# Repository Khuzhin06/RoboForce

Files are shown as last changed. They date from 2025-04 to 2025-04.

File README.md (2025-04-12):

# RoboForce

Всем привет! Давно хотели собрать своего робота? Не слышали про ROS? Не знаете с чего начать?

Тогда вы не зря зашли к нам, мы постараемся максимально подробно и быстро рассказать о нашем пути создания робота на ROS2 Jazzy и esp32,по этим материалам вы с легкостью сможете повторить этот проект. 

Ну а если вы хотите с головой погрузится в мир увлекательной робототехники и разобраться во всех тонкостях, то проходите курс на stepik - https://stepik.org/course/221157/syllabus Все материалы, используемые в этой статье были взяты из этого курса и мы лишь делимся опытом создания робота и проблемами с которыми столкнулись мы. 

Проблемы при сборки робота - это неотъемлемая часть процесса, поэтому мы постарались описать решение всех проблем с которыми мы сталкивались в процессе сборки и программирования робота.

Также много интересной, полезной и актуальной информации можете найти в нашем TG-канале https://t.me/RoboForc 

# Содержание:

[I модуль - Сборка робота](#i-модуль---сборка-робота)
- [1. Подготовка материалов и инструментов](#1-подготовка-материалов-и-инструментов)
- [2. Изготовление корпуса](#2-изготовление-корпуса)
  - [Шаг 1: Резка деталей](#шаг-1-резка-деталей)
  - [Шаг 2: 3D-печать](#шаг-2-3d-печать)
  - [Шаг 3: Сборка каркаса (первый слой)](#шаг-3-сборка-каркаса-первый-слой)
  - [Шаг 4: Сборка каркаса (средний слой)](#шаг-4-сборка-каркаса-средний-слой)
  - [Шаг 5: Соединение нижней и средней платформ](#шаг-5-соединение-нижней-и-средней-платформ)
  - [Шаг 6: Тестовый запуск](#шаг-6-тестовый-запуск)  

[II Модуль - Программировоние ESP32](#ii-модуль-программирование-esp32)
- [1. Настройка моторов](#1-настройка-моторов)
- [2. Загрузка основной программы на ESP32](#2-загрузка-основной-программы-на-esp32)  

[III Модуль - Настройка и программирование верхнего уровня](#iii-модуль-настройка-и-программирование-верхнего-уровня)
- [1. Установка ubuntu](#1-установка-ubuntu)
- [2. Установка ROS2](#2-установка-ros2)
- [3. Настройка необходимых пакетов](#3-настройка-необходимых-пакетов)

# I Модуль - Сборка робота

## 1. Подготовка материалов и инструментов
Необходимые инструменты:
- Лазерный резак – для резки фанеры
- Дрель и сверла (2–3мм) – для отверстий
- Набор отверток с разными насадками
- Паяльник (40 Вт) + припой (POS-60) – для электроники
- Мультиметр – проверка цепей
- Наждачка - для обработки краёв деталей после резки.

Материалы и комплектующие:  

| Компонент | Описание | Кол-во | Ссылка | Стоимость |
| --- | --- | --- | --- |--- |
| Фанера | Толщина 6 мм, 600х600 | 1 лист | https://www.ozon.ru/product/fanera-9-mm-sort-3-3-600h600-mm-1869700011/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 | 370 |
| Винты М3 (+ гайки М3)| 30шт х 20мм, 4шт х 30мм, 4шт х 50мм | 38 | https://aliexpress.ru/item/1005005552471765.html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 | 160 |
| Винты М2.5 (+ гайки М2.5) | 2шт х 10мм | 2 | https://aliexpress.ru/item/1005005552471765.html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 | 150 |
| Винты М2 (+ гайки М2)| 4 шт х 10мм | 4 | https://aliexpress.ru/item/1005005552471765.html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 | 120 |
| Муфты  | Необходимы для закрепления колес на валах моторов | 2 | https://aliexpress.ru/item/1005004333022107.html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 | 420 |
| OMNI-колесо | Позволяет двигаться роботу в любом направлении ьез поворота основных колес | 1 | https://aliexpress.ru/item/1005008405743640.html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 | 1540 |
| Микрокомпьютер Raspberry pi 5 8gb | «Верхний уровень». Обрабатывает информацию, поступающую с ESP (“нижнего уровня»). Поддержка новейших интерфейсов. Отлично подходит к задачам компьютерного зрения, обработки данных с лидаров.  | 1 | https://sl.aliexpress.ru/p?key=0vxkGbg | 10000 |
| Микроконтроллер ESP32-WROOM-32 | «Нижний уровень». Собирает информацию с датчиков, энкодеров и отправляет на «верхний уровень». Подходит для сетевого проекта из-за встроенных Wi-Fi и Bluetooth, высокой производительности и большого объёма памяти. | 1 | https://sl.aliexpress.ru/p?key=7oxkGZr | 300 |
| Моторы JGA25-370 77 RPM 12 B | Необходимы для передвижения робота. Используем 12В для упрощения питания. | 2 | https://aliexpress.ru/item/1005007793208347.html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 | 1200 |
| Драйвер моторов L298N | Необходим для управления моторов. | 1 | https://aliexpress.ru/item/1005007125159518.html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 | 150 |
| Понижающие DC-DC преобразователи Readytosky FPV RC UBEC 5V 5A | Обеспечивает стабильное питание для микроконтроллера, микрокомпьютера, датчиков и драйверов. Имеет удобный форм-фактор и изолированный корпус. | 2 | https://aliexpress.ru/item/33019505937.html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 | 530 |
| Литиевые батареи JOUYM 18650, 2000 мАч | Обеспечивает питание робота. Обладают высокой плотностью энергии при относительно небольшом размере. Можно последовательно соединять несколько штук, добиваясь нужного напряжения. | 3 | https://sl.aliexpress.ru/p?key=ajxkGkw | 460 |
| Держатель для батарей | Корпус для уставноки литейных батареек | 1 | https://aliexpress.ru/item/1005005586103501.html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 | 140 |
| Лидар SLAMTEC RPLIDAR C1 | «Глаза» робота, который смотрит на окружение, вычисляет расстояние на 360 градусов вокруг, определяет препятствия впереди | 1 | https://sl.aliexpress.ru/p?key=fmxkGwR | 6740 |
| Штыревые штекеры и гнезда | Служат для удобства работы с микроконтроллером, его легкой замены - провода припаиваются не к самому МК, а к штекерам. | 2х2 | https://aliexpress.ru/item/1005004954771161.html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 | 200 |
| Комплект разъемов | Нужны для соединения электронной схемы без пайки. | 1 | https://aliexpress.ru/item/1005007622670523.html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 | 120 |

СТОИМОСТЬ КОМПОНЕНТОВ ДЛЯ СБОРКИ РОБОТА:

За относительно небольшой бюджет можно также собрать достаточно надежного и производительного робота.
Суммируя все цены комплектующих из I модуля 1 пункта, мы получаем итоговую стоимость нашей модели - 22.600 рублей (на момент 06.04.2025).

## 2. Изготовление корпуса

### Шаг 1: Резка деталей
Загрузите DXF-файлы в станок лазерной резки.  
Основные детали:
- Основание (нижняя платформа)
- Средняя платформа
- Крышка (верхняя платформа)
- 2 опоры для OMNI колеса
- 5 стоек по 60 мм
- 4 стойки по 130 мм
После резки обработайте края наждачкой, чтобы избежать заусенцев.  

### Шаг 2: 3D-печать
Загрузите stl-файлы в станок 3D-печати.  
Основные детали:  
- 2 колеса
- Стойки для моторчиков



### Шаг 3: Сборка каркаса (первый слой)
1. Установка мотор редукторов
На валы мотор-редукторов установите колёса с помощью муфт (2 шт) и винтов М3 (2 шт), закрепите их стопорными винтами.


Найдите на нижней платформе посадочные места под моторы.
Зафиксируйте каждый мотор винтами M3 х 50 мм (4 шт) и гаек М3 (4 шт) с помощью напечатанных стоек (обратите внимание на то, чтобы провода от энкодеров были выведены к центру платформы)
Убедитесь, что при вращении колёса не задевают за край платформы и установлены ровно.
Уделите внимание ровной установке колес, это обеспечит качественное движение без лишних корректировок.



2. Установка OMNI колеса 
Найдите на нижней платформе посадочные места под вырезанные опоры OMNI колеса.
Установите их с помощью винтов М3 х 20 (4 шт) и гаек М3 (4 шт)



Закрепите OMNI колесо винтами М3 (2 шт).
Убедитесь, что при вращении колёсо не задевает за край платформы.

3. Установка драйвера моторов
Найдите в центре нижней платформы посадочные места под драйвер
Установите драйвер с помощью винтов М3 (2шт) и гаек М3 (2шт)


### Шаг 4: Сборка каркаса (средний слой)
1. Пайка шилда для ESP
Шилд – плата с контактными площадками.   
Установите на ESP штыревые гнезда, затем вставьте конструкцию в печатную плату (со стороны пайки)

Установите штыревые штекеры в средних с конструкцией линиях на плате.
Аккуратно переверните плату, поддерживая все компоненты.


Включите паяльник и дождитесь, пока инструмент разогреется до 300-350°C. 
Нанесите припой на крайние контакты (используйте флюс для лучшего растекания припоя)
Необходимо спаять все крайние контакты попарно (контакт гнезда с контактом штекера)
Проведите аналогичную работу со всеми оставшимися контактами (ВАЖНО: два спаянных контакты не должны быть соединены с соседними. 


После окончания пайки необходимо провести проверку: 
А. Визуальный осмотр:  
   - Нет ли перемычек между контактами (проверка на отсутствие короткого замыкания)
 Все ли дорожки пропаяны (особенно у штыревых разъёмов).  
Б.  Тест мультиметром:  
   - Прозвоните линии 5V и 3.3V на КЗ.  
   - Проверьте контакты GPIO на обрыв.

2. Установка шилда на платформу
Найдите на средней платформе посадочное место для шилда
Вставьте снизу в платформу винты М2 (4шт) и накрутите на них гайки М2 (4шт). Данная конструкция не позволит передать находящиеся под шилдом провода  
Установите на винты собранный шилд и закрепите его сверху гайками М2 (4шт)


3. Установка блока питания
Найдите на средней платформе посадочное место для блока питания (средняя часть платформы) 
Закрепите блок с помощью винтов М3 (2 шт) и гаек М3 (2шт)  (ВАЖНО: провода должны выходить в центральную часть платформы)


4. Монтаж:
   макетную и монтажную схему можно подробно изучить в папке Electronic scheme
Электрическая схема:


Пайка проводов, преобразователей, RGB ленты, драйвера, энкодеров, микроконтроллера.
Залудите контакты перед пайкой, а затем работайте по тому же принципу, как и при пайке шилда  
После окончания пайки необходимо провести проверку (визуальный осмотр и тест мультиметром) (ВАЖНО: проверьте, нет ли пережатых проводов)



### Шаг 5: Соединение нижней и средней платформ
Соберите стойки из фанеры: 5 штук по 60 мм, 4 штуки по 130 мм (для этого понадобятся гайки М3 18 шт)
Соедините нижнюю и верхнюю платформы с помощью стоек по 60 мм, винтов М3 (10шт)






### Шаг 6: Тестовый запуск
- Подключите питание. 
- Проверьте работу моторов, питание и загрузку ESP.
- Проанализируйте, движится ли робот в заданном вами направлении или нет.
ВАЖНО: есть вероятность, что робот поедет в обратную сторону, так как у него 2 шнура, которые можно перепутать местами. В таком случае необходимо поменять местами номера бортов в коде и загрузить его. Теперь робот поедет в заданном вами направлении.
- Измерьте количество тиков и запишите их в программу.


![Uploading image.png…]()

# II Модуль - Программирование ESP32

После того как вся аппаратная часть собрана, можно переходить и к программной.
Все действия лучше делать на ноутбуке - так как это будет быстрее и надежней, хотя в теории можете и сделать все тоже самое на raspberry.
Начнем с программирования "нижнего уровня", тоесть esp32. Программировать будем через arduino IDE (если она еще у вас не установлена, то можете скачать с официального сайта https://www.arduino.cc/en/software ).
Чтоб можно было прошивать нашe платe добавим ее в список доступных для прошивки. Нужно зайти в файл->настройки и в поле "Дополнительные менеджеры плат" вставляем ссылку: https://raw.githubusercontent.com/espressif/arduino-esp32/gh-pages/package_esp32_index.json и нажимаем "ОК". 
После заходим в инструменты->плата->менеджер плат тут в строке поиска вводим esp32, выбираем соответсвующий вариант снизу и нажимаем на кнопку установить. 
После всех этих процедур для прошивки станут доступны платы семейства  ESP32.  Чтоб выбрать нужную плату заходим в инструменты->esp32 и выбираем нужную плату (мы использовали "ESP32 dev Module"). Также необходимо подключить саму плату к компьютеру и выбрать порт к которому она подключена заходим опять в инструменты->порт и выбираем нужный порт.
Помимо этого необходимо установить библиотеку для адресной светодиодной ленты. Для этого заходим в скетч->подключить библиотеку->Управлять библиотеками в поле поиска вводим "neopixel" и выбираем Adafruit neopixel и нажимаем установить.

## 1. Настройка моторов

Здесь нам нужно понять как подключены моторы и сделать так, чтоб робот ехал вперед, когда мы действительно этого хотим.

-проверить направление вращения моторов
-проверить подключение энкодеров

Скачиваем или копируем код для esp32 из папки low_level "test_move_esp32", открфываем этот код в arduino ide и нажимаем в правом верхнем углу "загрузить".

После полной загрузки кода колеса робота должны вращаться вперед, если это не так, то следует поменять в коде местами номера пинов, к которым подключён драйвер моторов левой или право стороны.
Для определения вращения энкодеров открываем в arduino IDE serial port и следим за значениями: оба значения на левом и правом моторах должны возрастать, если это не так, то меняем местами пины энкодера в программе.

## 2. Загрузка основной программы на ESP32.

Для этого шага нам необходимо скопировать все параметры из прдыдущего кода, а также измерить диаметр колеса и расстояние между центрами колёс.
Все эти параметры вашего робота необходимо внести в скетч main_esp32.ino, который находится в папке low-level. Этот код вы также скачиваете (или копируете) и открываете в Arduino IDE для дальнейшей прошивки. После внесения всех изменений в вашу программу по аналогии с 1 шагом загружаем программу на  микроконтроллер.

# III Модуль - Настройка и программирование верхнего уровня

До запуска робота остался последний и самый ответственный шаг. Настройка микрокомпьютера - наших "мозгов" робота. В нашем проекте эту роль выполняла raspberry pi 5 8gb, поэтому советуем все повторять на таком же железе для предотвращения проблем. Безусловно, подойдет и другое железо, по типу repka pi, orange pi, banana pi и подобных "фруктов". Но наиболее популярной и поддерживаемой всетаки остается "малинка".

## 1. Установка ubuntu

По сути raspberry pi является аналогом вашего ноутбука или настольного компьютера, но куда меньших размеров и, скорее всего, хуже по вычислительным мощностям. Но тем не менее нам нужно поставить на наш микрокомпьютер операционную систему - наиболее подходящая ubuntu 24.04. !!! при сборке нашего робота мы сначала поставили 24.10 - по принципу: больше - лучше, но тут,увы, так не работает. И чтобы у вас без проблем все встало как нужно необходимо использовать именно ubuntu 24.04 LTS!!! 
Скачать ее можно с официального сайта - она абсолютно бесплатная. После загрузки образа диска необходимо его записать на sd карту, которая будет стоять в малинке. Мы использовали на 64гб. Или же можно сразу скачать Raspberry PI Imager(https://www.raspberrypi.com/software/) и там уже в интерфейсе выбрать нужную операционную систему и ваш носитель.

## 2. Установка ROS2

После установки и базовых настроек операционной системы можно установить и сам ros2 jazzy (в нашем проекте используется десктопная версия ros-jazzy-desktop), лучше всего брать команды для установки с официального сайта (https://docs.ros.org/en/jazzy/Installation/Ubuntu-Install-Debs.html), так как они могут меняться. 

Если установить не получается пробуем еще раз, внимательно копируем все и вставляем в терминал. Если совсем не помогает, то можно попытаться погуглить ошибку, которую вам выдает терминал или же переустановить заново операционку на флешку и убедится что это точно ubuntu 24.04 LTS.

Также установим еще пару пакетов:

```
sudo apt install python3-pip
```

```
pip3 install setuptools
```

```
sudo apt install python3-colcon-common-extensions
```

## 3. Настройка необходимых пакетов

После установки ros2 в домашнеq директории нужно создать папку где будут хранится все наши пакеты для ros2.

```
mkdir ros2_ws
```

```
cd ros2_ws
```

```
mkdir src
```

```
cd-
```

```
colcon build
```

после создания нашего рабочего пространства
создадим пакет, который будет считывать сообщения из топика /cmd_vel

```
cd ~/ros2_ws/src
ros2 pkg create robot_control --build-type ament_python --dependencies rclpy geometry_msgs
cd robot_control/robot_control
```

создаем файл robot_controller_node.py и копируем в него код из одноименного файла папки high_level. Предварительно также нужно подключить прошитую esp32 к одному из портов raspberry pi, а затем ввести команду: 
```
ls -l /dev/serial/by-path/
```

после необходимо скопировать путь и заменить его в коде.
сохраняем файл. Делаем скрипт исполняемым:
```
chmod +x robot_controller_node.py
```

Далее находим и редактируем файл setup.py в этом пакете (нужно добавить 3-ю строчку):

```
entry_points={
    'console_scripts': [
        'robot_controller_node = robot_control.robot_controller_node:main',
    ],
},
```

Затем пересоберем наш пакет и установим все зависимости:

```
cd ~/ros2_ws
colcon build
source install/setup.bash
```

И запускаем наш пакет:

```
ros2 run robot_control robot_controller_node
```

Проверяем список топиков в другом терминале, должен появиться топик /cmd_vel

```
source /opt/ros/jazzy/setup.bash
ros2 topic list
```

Если топик появился, то все прошло успешно и мы можем управлять нашим роботом с клавиатуры!

Для этого установим пакет:

```
sudo apt install ros-jazzy-teleop-twist-keyboard
```
И запускаем пакет: 
```
ros2 run teleop_twist_keyboard teleop_twist_keyboard
```
Теперь робот должен ехать! Поздравляю мы проделали большой путь и запустили робота!

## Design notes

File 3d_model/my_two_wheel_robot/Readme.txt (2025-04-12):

Для запуска пакета его нужно скачать в директорию ros2_ws/src/. Затем в директории ros2_ws/ выполнить сборку пакета командой - colcon build, и подключив все зависимости - source install/setup.bash и source /opt/ros/jazzy/setup.bash , затем запустить сам пакет: ros2 launch my_two_wheel_robot two_wheel_robot.launch.py

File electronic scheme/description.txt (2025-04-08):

В данном документе можно изучить принципиальную, монтажную и макетную схему электронной цепи нашей модели робота 

  1 На макетной схеме вы сможете увидеть все комплектующие и их подключение

  2 На монтажной сможете увидеть их расположение между собой в самом роботе

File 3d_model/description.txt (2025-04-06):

Для разработки данной моедли робота необходимо:
 1) Распечатать 3D модели для колесной базы:
        а) колеса - 2 штуки
        б) крепежи для колес верхние - 2 штуки
        в) крепежи для колес нижние - 2 штуки
 2) вырезать корпус робота:
        а) основание 1 этажа робота

        б) основания 2 и 3 этажа робота ( 2 штуки)

        в)элемент стойки ( 9 пар по 2 штуки)

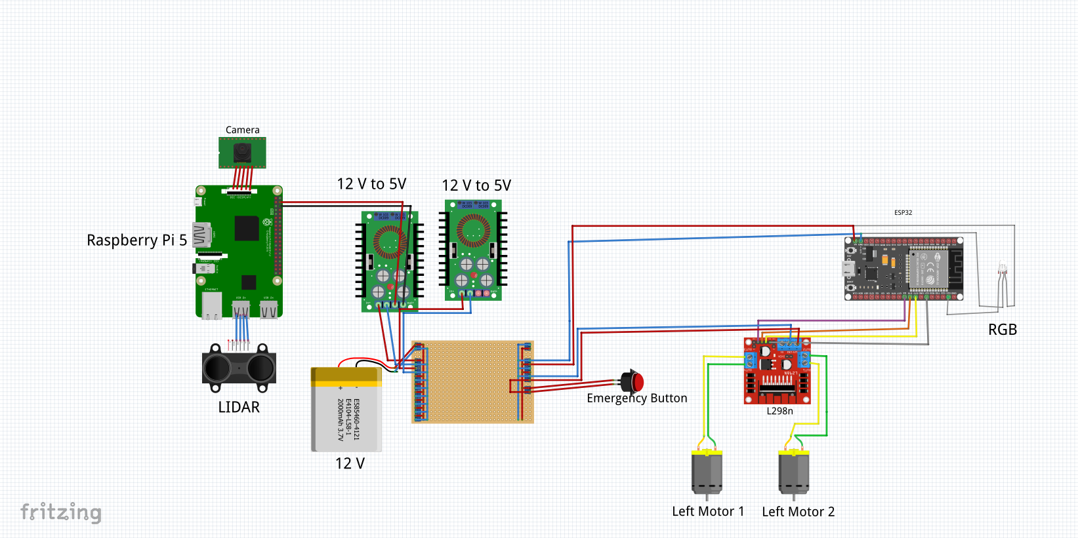
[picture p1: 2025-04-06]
electronic scheme/electronic_schem.png

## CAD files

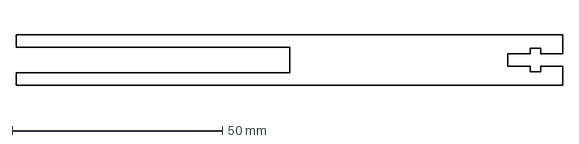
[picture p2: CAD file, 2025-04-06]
3d_model/6mm/LayerSupport130.dxf
130.0 x 12.0 mm

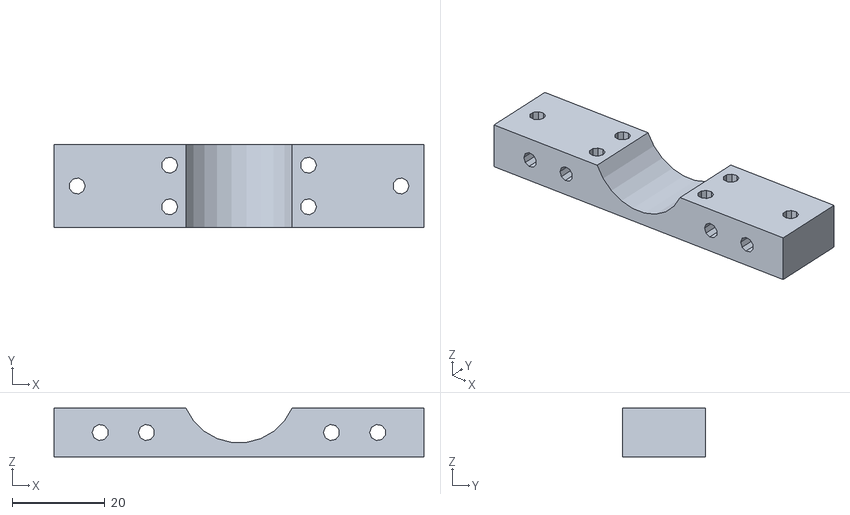
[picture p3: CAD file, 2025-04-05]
3d_model/krep_motor_niz_RoboForce.stl
80.0 x 18.0 x 10.5

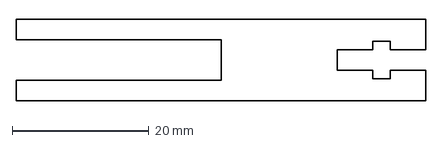
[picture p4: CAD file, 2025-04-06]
3d_model/6mm/LayerSupport65.dxf
60.0 x 12.0 mm

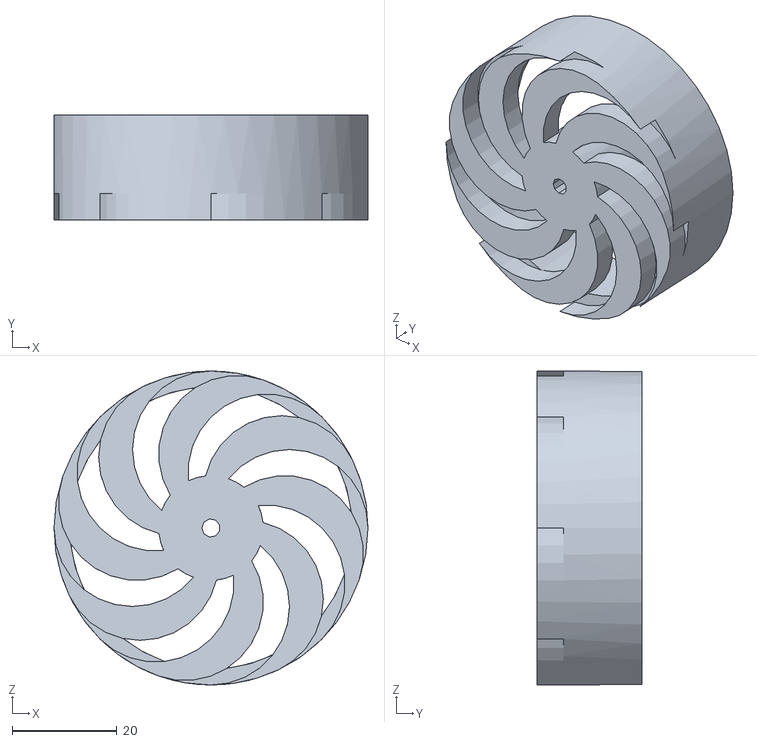
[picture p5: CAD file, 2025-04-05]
3d_model/wheel_RoboForce.stl
60.0 x 20.0 x 60.0

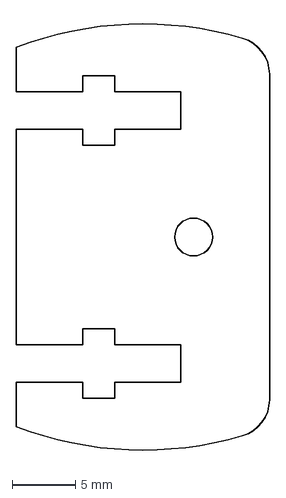
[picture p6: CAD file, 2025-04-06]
3d_model/6mm/OMNISupport.dxf
20.0 x 34.9 mm

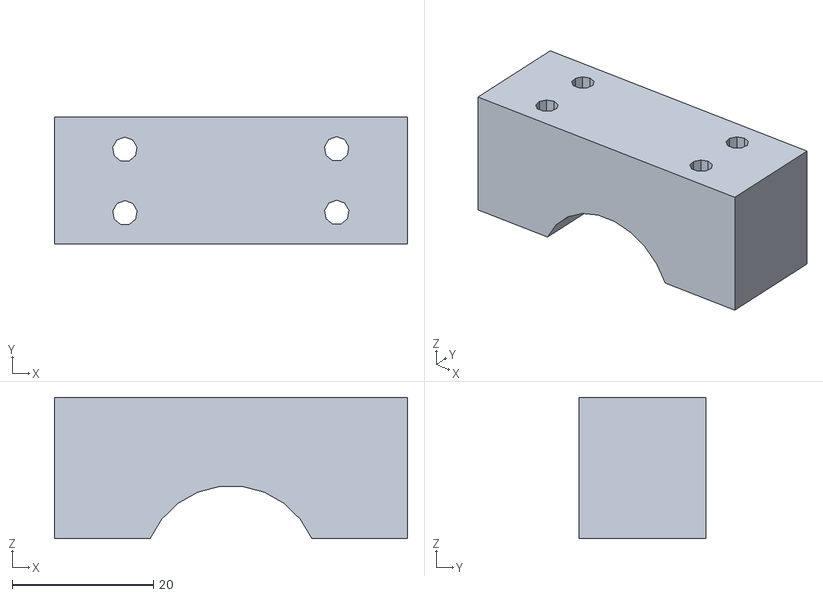
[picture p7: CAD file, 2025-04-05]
3d_model/krepMotor_verh_RoboForce.stl
50.0 x 18.0 x 20.0

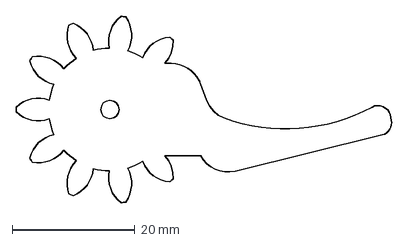
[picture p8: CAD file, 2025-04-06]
3d_model/6mm/GripperRightGear.dxf
61.4 x 30.4 mm

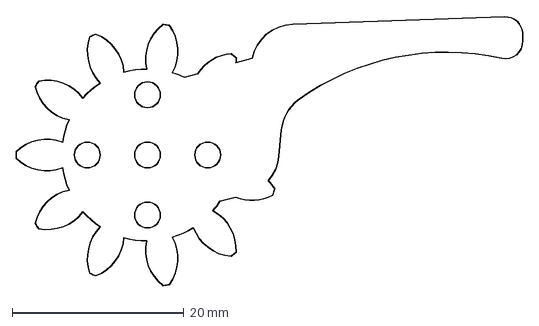
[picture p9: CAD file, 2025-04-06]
3d_model/6mm/GripperLeftGear.dxf
59.0 x 31.3 mm

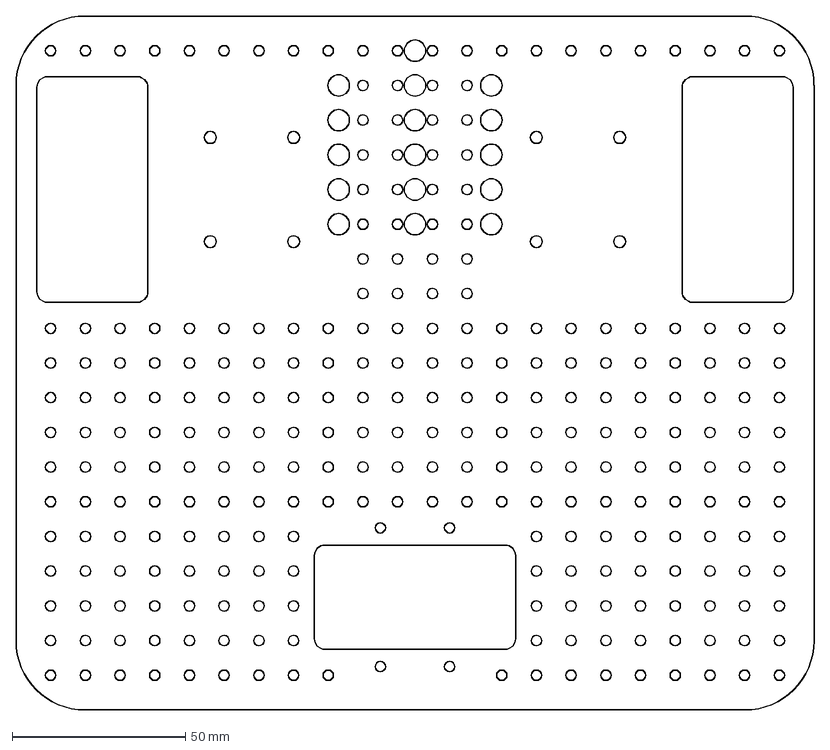
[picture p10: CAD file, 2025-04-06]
3d_model/6mm/BaseLayer.dxf
230.0 x 200.0 mm

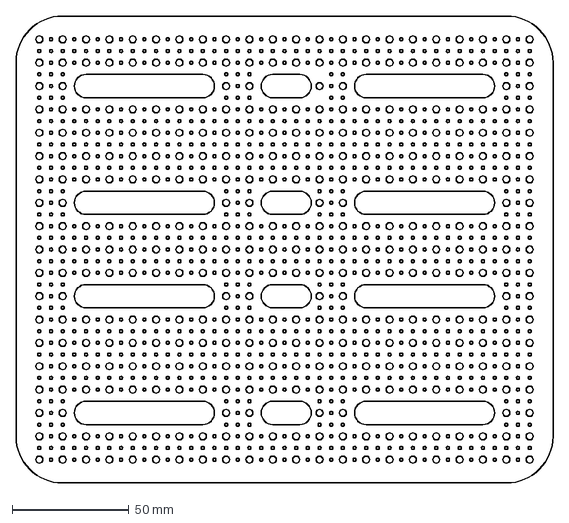
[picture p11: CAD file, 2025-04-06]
3d_model/6mm/Layer.dxf
230.0 x 200.0 mm

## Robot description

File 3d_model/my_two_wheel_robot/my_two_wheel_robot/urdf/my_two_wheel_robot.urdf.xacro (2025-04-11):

<?xml version="1.0"?>
<robot name="visual">

  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
  <link name="odom"/>

  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
  <link name="base_link">
    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
    <inertial>
      <mass value="1.5"/>
      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
    </inertial>
  </link>
  <joint name="base_link_joint" type="fixed">
    <parent link="odom"/>
    <child link="base_link"/>
    <origin xyz="0 0 0" rpy="0 0 0"/>
  </joint>
  
    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
  <link name="rod_front_left">
    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
    <inertial>
      <mass value="0.05"/>
      <origin xyz="0.09 0.105 0.095" rpy="0 0 0"/>
      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
    </inertial>
  </link>
  <joint name="rod_front_left_joint" type="fixed">
    <parent link="base_link"/>
    <child link="rod_front_left"/>
    <origin xyz="0 0 0" rpy="0 0 0"/>
  </joint>

  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
  <link name="rod_front_right">
    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
    <inertial>
      <mass value="0.05"/>
      <origin xyz="0.09 -0.105 0.095" rpy="0 0 0"/>
      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
    </inertial>
  </link>
  <joint name="rod_front_right_joint" type="fixed">
    <parent link="base_link"/>
    <child link="rod_front_right"/>
    <origin xyz="0 0 0" rpy="0 0 0"/>
  </joint>

  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
  <link name="rod_rear_left">
    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
    <inertial>
      <mass value="0.05"/>
      <origin xyz="-0.09 0.105 0.095" rpy="0 0 0"/>
      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
    </inertial>
  </link>
  <joint name="rod_rear_left_joint" type="fixed">
    <parent link="base_link"/>
    <child link="rod_rear_left"/>
    <origin xyz="0 0 0" rpy="0 0 0"/>
  </joint>

  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
  <link name="rod_rear_right">
    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
    <inertial>
      <mass value="0.05"/>
      <origin xyz="-0.09 -0.105 0.095" rpy="0 0 0"/>
      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
    </inertial>
  </link>
  <joint name="rod_rear_right_joint" type="fixed">
    <parent link="base_link"/>
    <child link="rod_rear_right"/>
    <origin xyz="0 0 0" rpy="0 0 0"/>
  </joint>

  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
  <link name="left_base">
    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
  </link>
  <joint name="left_base_joint" type="fixed">
    <parent link="base_link"/>
    <child link="left_base"/>
    <origin xyz="0.05 0.13 0" rpy="0 0 0"/>
  </joint>
  <link name="left_wheel">
    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
    <inertial>
      <mass value="1"/>
      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
    </inertial>
  </link>
  <joint name="left_wheel_joint" type="continuous">
    <axis xyz="0 1 0"/>
    <parent link="left_base"/>
    <child link="left_wheel"/>
    <origin xyz="0 0 0" rpy="0 0 0"/>
    <command_interface name="velocity"/>
    <state_interface name="position"/>
    <state_interface name="velocity"/>
  </joint>

  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
  <link name="right_base">
    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
  </link>
  <joint name="right_base_joint" type="fixed">
    <parent link="base_link"/>
    <child link="right_base"/>
    <origin xyz="0.05 -0.13 0" rpy="0 0 0"/>
  </joint>
  <link name="right_wheel">
    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
    <inertial>
      <mass value="1"/>
      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
    </inertial>
  </link>
  <joint name="right_wheel_joint" type="continuous">
    <axis xyz="0 1 0"/>
    <parent link="right_base"/>
    <child link="right_wheel"/>
    <origin xyz="0 0 0" rpy="0 0 0"/>
    <command_interface name="velocity"/>
    <state_interface name="position"/>
    <state_interface name="velocity"/>
  </joint>

  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
  <link name="caster_wheel">
    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
    <inertial>
      <mass value="0.1"/>
      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
    </inertial>
  </link>
  <joint name="caster_wheel_joint" type="fixed">
    <parent link="base_link"/>
    <child link="caster_wheel"/>
    <origin xyz="-0.09 0 -0.01" rpy="0 0 0"/>
  </joint>

  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
  <link name="electronics_plate">
    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
    <inertial>
      <mass value="0.3"/>
      <origin xyz="0 0 0.0025" rpy="0 0 0"/>
      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
    </inertial>
  </link>
  <joint name="electronics_plate_joint" type="fixed">
    <parent link="base_link"/>
    <child link="electronics_plate"/>
    <origin xyz="0 0 0.065" rpy="0 0 0"/>
  </joint>

  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
  <link name="top_plate">
    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
    <inertial>
      <mass value="0.8"/>
      <origin xyz="0 0 0.0025" rpy="0 0 0"/>
      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
    </inertial>
  </link>
  <joint name="top_plate_joint" type="fixed">
    <parent link="electronics_plate"/>
    <child link="top_plate"/>
    <origin xyz="0 0 0.130" rpy="0 0 0"/>
  </joint>

  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
  <joint name="arm_shoulder_joint" type="revolute">
    <parent link="top_plate"/>
    <child link="arm_link1"/>
    <origin xyz="0.1 0 0" rpy="0 0 0"/>
    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
    <axis xyz="0 1 0"/>
    <limit lower="-1.57" upper="1.57" effort="5.0" velocity="1.0"/>
  </joint>

  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
  <link name="arm_link1">
    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
    <inertial>
      <mass value="0.2"/>
      <origin xyz="0 0 -0.04" rpy="3.1416 0 0"/>
      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
    </inertial>
  </link>

  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
  <joint name="arm_elbow_joint" type="revolute">
    <parent link="arm_link1"/>
    <child link="arm_link2"/>
    <origin xyz="0 0 -0.08" rpy="0 0 0"/>
    <axis xyz="0 1 0"/>
    <limit lower="0" upper="2.8" effort="5.0" velocity="1.0"/>
  </joint>

  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
  <link name="arm_link2">
    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
    <inertial>
      <mass value="0.2"/>
      <origin xyz="0 0 -0.04" rpy="3.1416 0 0"/>
      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
    </inertial>
  </link>

  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
  <joint name="wrist_joint" type="fixed">
    <parent link="arm_link2"/>
    <child link="gripper_base"/>
    <origin xyz="0 0 -0.08" rpy="0 0 0"/>
  </joint>

  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
<link name="gripper_base">
  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
  <inertial>
    <mass value="0.1"/>
    <origin xyz="0 0 0" rpy="0 0 0"/>
    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
  </inertial>
</link>

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
<link name="finger_left">
  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
  <inertial>
    <mass value="0.01"/>
    <origin xyz="0 0.025 -0.015" rpy="0 0 90"/>
    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
  </inertial>
</link>
<joint name="finger_left_joint" type="revolute">
  <parent link="gripper_base"/>
  <child link="finger_left"/>
  <origin xyz="0 0 -0.01" rpy="0 0 0"/>
  <axis xyz="-1 0 0"/>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
  <limit lower="0" upper="0.5" effort="2.0" velocity="1.0"/>
</joint>

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
<link name="finger_right">
  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
  <inertial>
    <mass value="0.01"/>
    <origin xyz="0 -0.025 -0.015" rpy="0 0 90"/>
    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
  </inertial>
</link>
<joint name="finger_right_joint" type="revolute">
  <parent link="gripper_base"/>
  <child link="finger_right"/>
  <origin xyz="0 0 -0.01" rpy="0 0 0"/>
  <axis xyz="1 0 0"/>
  <limit lower="0" upper="0.5" effort="2.0" velocity="1.0"/>
</joint>

  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
  <link name="lidar_link">
    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
    <inertial>
      <mass value="0.2"/>
      <origin xyz="0 0 0.04" rpy="0 0 0"/>
      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
    </inertial>
  </link>
  <joint name="lidar_joint" type="fixed">
    <parent link="top_plate"/>
    <child link="lidar_link"/>
    <origin xyz="0 0 0" rpy="0 0 0"/>
  </joint>

  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
  <ros2_control name="my_robot_hardware" type="system">
    <hardware>
      <plugin>mock_components/GenericSystem</plugin>
      <param name="update_rate" type="int">50</param>
      <param name="calculate_dynamics" type="bool">true</param>
    </hardware>
    <joint name="left_wheel_joint">
      <command_interface name="velocity"/>
      <state_interface name="position"/>
      <state_interface name="velocity"/>
    </joint>
    <joint name="right_wheel_joint">
      <command_interface name="velocity"/>
      <state_interface name="position"/>
      <state_interface name="velocity"/>
    </joint>
  </ros2_control>

</robot>

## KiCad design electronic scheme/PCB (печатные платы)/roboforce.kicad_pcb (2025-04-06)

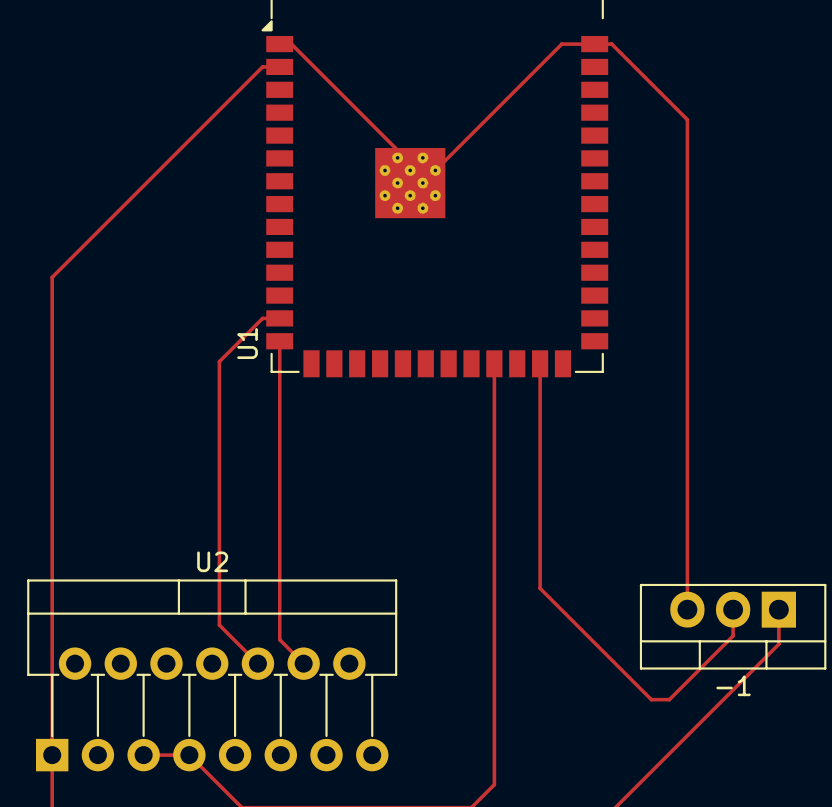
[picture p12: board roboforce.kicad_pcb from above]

Board: 2 copper layers, 3 parts (0 on the bottom side), 6 nets.

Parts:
-1: -; TO-220-3_Vertical
U1: ESP32-S3-WROOM-1
U2: L298N; TO-220-15_P2.54x2.54mm_StaggerOdd_Lead4.58mm_Vertical

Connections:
unnamed: -1.3 (GND), U1.1 (GND), U1.40 (GND), U1.41 (GND)
unnamed: -1.1 (VA), U1.2 (3V3), U2.1 (SENSE_A)
unnamed: -1.2 (VB), U1.25 (IO48)
unnamed: U1.20 (IO12), U1.23 (IO21), U2.5 (IN1), U2.7 (IN2)
unnamed: U1.13 (IO19), U2.10 (IN3)
unnamed: U1.14 (IO20), U2.12 (IN4)

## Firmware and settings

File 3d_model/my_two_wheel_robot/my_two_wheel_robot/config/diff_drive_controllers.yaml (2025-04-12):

# Параметры менеджера контроллеров ROS 2 Control
controller_manager:
  ros__parameters:
    update_rate: 50               # Частота обновления контроллеров (Гц)
    
    joint_state_broadcaster:
      type: joint_state_broadcaster/JointStateBroadcaster
      publish_rate: 50.0
    # Описание контроллера дифференциального привода
diff_drive_controller:
  ros__parameters:
    type: diff_drive_controller/DiffDriveController
    left_wheel_names: ["left_wheel_joint"]
    right_wheel_names: ["right_wheel_joint"]
    wheel_separation: 0.26      # Расстояние между колесами, м
    wheel_radius: 0.0325          # Радиус колес, м 
    base_frame_id: base_link    # Имя фрейма базы робота
    odom_frame_id: odom         # Имя фрейма одометрии
    publish_rate: 50.0          # Частота публикации одометриии (Hz)
    cmd_vel_timeout: 0.5        # Таймаут (сек) сброса скорости при отсутствии команд
    # Лимиты скоростей/ускорений (пример):
    linear.x.has_velocity_limits: true
    linear.x.max_velocity: 2.0   # м/с
    angular.z.has_velocity_limits: true
    angular.z.max_velocity: 2.0  # рад/с
      # Примечание: В ROS2 Jazzy контроллер ожидает TwistStamped, см. шаг 5
    # Описание широковещательного контроллера состояний суставов

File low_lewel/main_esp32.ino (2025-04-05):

#include <Adafruit_NeoPixel.h>

// ------------------------- НАСТРОЙКИ СВЕТОДИОДНОЙ ЛЕНТЫ -------------------------
#define PIN_WS2812B 23     // Пин, к которому подключена лента
#define NUM_PIXELS 50      // Кол-во светодиодов в ленте
#define LED_BRIGHTNESS 30                               // Базовая «глобальная» яркость (0-255), если нужно

Adafruit_NeoPixel ws2812b(NUM_PIXELS, PIN_WS2812B, NEO_GRB + NEO_KHZ800);

uint8_t bootMode = 1;
// ---------------------------------------------------------------------------------

/****************************************************************************
 * Определение пинов, переменных энкодеров, положения робота и т.д.
 ***************************************************************************/
#define LEFT_MOTOR_A  19   // Цифровой выход (левый мотор). Если 0 - едем вперед
#define LEFT_MOTOR_B  21 // Цифровой выход (левый мотор). Если 0 - едем назад
#define RIGHT_MOTOR_A 18  // Цифровой выход (правый мотор). Если 0 - едем вперед
#define RIGHT_MOTOR_B 5  // Цифровой выход (правый мотор). Если 0 - едем назад

#define LEFT_ENCODER_A 12    // Цифровой вход, канал A энкодера левого колеса
#define LEFT_ENCODER_B  14   // Цифровой вход, канал B энкодера левого колеса 
#define RIGHT_ENCODER_A 26   // Цифровой вход, канал A энкодера правого колеса
#define RIGHT_ENCODER_B 27 

volatile long left_encoder_value = 0;
volatile long right_encoder_value = 0;
long last_left_encoder = 0;
long last_right_encoder = 0;

long last_speed_left_encoder = 0, last_speed_right_encoder = 0;
float vlSpeedFiltered = 0.0, vrSpeedFiltered = 0.0;
uint32_t lastTimeL = 0, lastTimeR = 0;

float targetLeftWheelSpeed = 0, targetRightWheelSpeed = 0;

float xPos = 0.0, yPos = 0.0, theta = 0.0;

const float WHEEL_DIAMETER = 70.0;       // мм
const float WHEEL_BASE = 180.0;          // мм (расстояние между центрами колёс)
const float ENCODER_RESOLUTION = 820.0;  // тиков на оборот
const float TICKS_TO_MM = (PI * WHEEL_DIAMETER) / ENCODER_RESOLUTION;
const float ALPHA = 0.5;  // Коэффициент экспоненциальной фильтрации скорости

// Глобальные коэффициенты PID – их можно обновлять через UART
float pidKp = 1.1;
float pidKi = 1.3;
float pidKd = 0.01;
float pidKff = 0.25;

// Глобальные PID-состояния
float errorLeftIntegral = 0;
float errorRightIntegral = 0;
float prevErrorLeft = 0;
float prevErrorRight = 0;
uint32_t lastPIDTime = 0;

// Функция сброса PID-переменных (интегральная и дифференциальная составляющие, а также фильтрованные скорости)
void resetPID() {
  errorLeftIntegral = 0;
  errorRightIntegral = 0;
  prevErrorLeft = 0;
  prevErrorRight = 0;
  vlSpeedFiltered = 0;
  vrSpeedFiltered = 0;
  lastPIDTime = millis();
}

/****************************************************************************
 * Переменные компенсации прямолинейного движения
 ***************************************************************************/
bool goingStraight = false;  // Флаг, указывающий, что робот едет прямо (угловая скорость ≈ 0)
long leftBase = 0;           // Значение left_encoder_value в момент начала прямолинейного движения
long rightBase = 0;          // Значение right_encoder_value в момент начала прямолинейного движения

/****************************************************************************
 * Прерывания энкодеров
 ***************************************************************************/
void left_interrupt() {
  digitalRead(LEFT_ENCODER_B) ? left_encoder_value++ : left_encoder_value--;
}
void right_interrupt() {
  digitalRead(RIGHT_ENCODER_B) ? right_encoder_value++ : right_encoder_value--;
}

/****************************************************************************
 * Одометрия
 ***************************************************************************/
void updateOdometry() {
  long deltaLeft = left_encoder_value - last_left_encoder;
  long deltaRight = right_encoder_value - last_right_encoder;
  last_left_encoder = left_encoder_value;
  last_right_encoder = right_encoder_value;

  float distLeft = deltaLeft * TICKS_TO_MM;
  float distRight = deltaRight * TICKS_TO_MM;
  float deltaS = (distLeft + distRight) / 2.0;
  float deltaTheta = (distRight - distLeft) / WHEEL_BASE;

  theta += deltaTheta;
  xPos += deltaS * cos(theta);
  yPos += deltaS * sin(theta);
}

/****************************************************************************
 * Вычисление скорости колес
 ***************************************************************************/
void computeSpeed() {
  uint32_t now = micros();
  if (lastTimeL == 0 || lastTimeR == 0) {
    lastTimeL = now;
    lastTimeR = now;
    last_speed_left_encoder = left_encoder_value;
    last_speed_right_encoder = right_encoder_value;
    return;
  }
  float dtL = (now - lastTimeL) * 1e-6f;
  float dtR = (now - lastTimeR) * 1e-6f;

  if (dtL > 0 && left_encoder_value != last_speed_left_encoder) {
    long deltaLeft = left_encoder_value - last_speed_left_encoder;
    float wlSpeed = ((float)deltaLeft / ENCODER_RESOLUTION) * 360.0f / dtL;
    float vlSpeed = (wlSpeed / 360.0f) * (PI * WHEEL_DIAMETER);
    vlSpeedFiltered = ALPHA * vlSpeed + (1.0f - ALPHA) * vlSpeedFiltered;
    last_speed_left_encoder = left_encoder_value;
    lastTimeL = now;
  } else if (dtL > 0.005 && left_encoder_value == last_speed_left_encoder) {
    vlSpeedFiltered = 0;
  }
  if (dtR > 0 && right_encoder_value != last_speed_right_encoder) {
    long deltaRight = right_encoder_value - last_speed_right_encoder;
    float wrSpeed = ((float)deltaRight / ENCODER_RESOLUTION) * 360.0f / dtR;
    float vrSpeed = (wrSpeed / 360.0f) * (PI * WHEEL_DIAMETER);
    vrSpeedFiltered = ALPHA * vrSpeed + (1.0f - ALPHA) * vrSpeedFiltered;
    last_speed_right_encoder = right_encoder_value;
    lastTimeR = now;
  } else if (dtR > 0.005 && right_encoder_value == last_speed_right_encoder) {
    vrSpeedFiltered = 0;
  }
}

/****************************************************************************
 * PID-регулятор для колес с компенсацией прямолинейного движения
 ***************************************************************************/
void computeWheelsPID() {
  const float integralLimit = 30.0;
  static float lastTargetLeft = 0.0;
  static float lastTargetRight = 0.0;

  // Если целевая скорость изменилась или установлена остановка – сброс PID
  if (targetLeftWheelSpeed != lastTargetLeft) {
    lastTargetLeft = targetLeftWheelSpeed;
  }
  if (targetRightWheelSpeed != lastTargetRight) {
    lastTargetRight = targetRightWheelSpeed;
  }
  if (targetLeftWheelSpeed == 0 && targetRightWheelSpeed == 0) {
    resetPID();
  }

  uint32_t now = millis();
  float dt = (now - lastPIDTime) / 1000.0f;
  if (dt < 0.001f) dt = 0.001f;
  lastPIDTime = now;

  // Вычисляем ошибки между целевыми и измеренными скоростями
  float errorLeft = targetLeftWheelSpeed - vlSpeedFiltered;
  float errorRight = targetRightWheelSpeed - vrSpeedFiltered;

  errorLeftIntegral += errorLeft * dt;
  errorRightIntegral += errorRight * dt;
  if (errorLeftIntegral > integralLimit) errorLeftIntegral = integralLimit;
  if (errorLeftIntegral < -integralLimit) errorLeftIntegral = -integralLimit;
  if (errorRightIntegral > integralLimit) errorRightIntegral = integralLimit;
  if (errorRightIntegral < -integralLimit) errorRightIntegral = -integralLimit;

  float derivativeLeft = (errorLeft - prevErrorLeft) / dt;
  float derivativeRight = (errorRight - prevErrorRight) / dt;
  prevErrorLeft = errorLeft;
  prevErrorRight = errorRight;

  float pidLeft = pidKp * errorLeft + pidKi * errorLeftIntegral + pidKd * derivativeLeft;
  float pidRight = pidKp * errorRight + pidKi * errorRightIntegral + pidKd * derivativeRight;

  float outputLeft = pidLeft + pidKff * targetLeftWheelSpeed;
  float outputRight = pidRight + pidKff * targetRightWheelSpeed;

  // --- Компенсация прямолинейного движения ---
  if (goingStraight && fabs(targetLeftWheelSpeed) > 1.0 && fabs(targetRightWheelSpeed) > 1.0) {
    // Вычисляем накопленное смещение от базового значения, зафиксированного при старте прямолинейного движения
    long leftTicks = left_encoder_value - leftBase;
    long rightTicks = right_encoder_value - rightBase;
    long diff = leftTicks - rightTicks;  // если diff > 0, левое колесо продвинулось дальше
    float KencStraight = 3.0f;           // Подберите опытным путём
    float corr = KencStraight * (float)diff;
    // Применяем корректировку: по 50% для каждого колеса
    outputLeft -= corr * 0.5f;
    outputRight += corr * 0.5f;
  }
  // --- Конец компенсации ---

  int leftA_PWM = 0, leftB_PWM = 0;
  int rightA_PWM = 0, rightB_PWM = 0;

  if (outputLeft >= 0) {
    leftA_PWM = 0;
    leftB_PWM = constrain((int)outputLeft, 0, 255);
  } else {
    leftA_PWM = constrain((int)(-outputLeft), 0, 255);
    leftB_PWM = 0;
  }
  if (outputRight >= 0) {
    rightA_PWM = 0;
    rightB_PWM = constrain((int)outputRight, 0, 255);
  } else {
    rightA_PWM = constrain((int)(-outputRight), 0, 255);
    rightB_PWM = 0;
  }

  setMotorsPWM(leftA_PWM, leftB_PWM, rightA_PWM, rightB_PWM);
}

/****************************************************************************
 * Функция управления моторами (вывод ШИМ)
 ***************************************************************************/
void setMotorsPWM(int leftA, int leftB, int rightA, int rightB) {
  leftA = constrain(leftA, 0, 255);
  leftB = constrain(leftB, 0, 255);
  rightA = constrain(rightA, 0, 255);
  rightB = constrain(rightB, 0, 255);
  analogWrite(LEFT_MOTOR_A, leftA);
  analogWrite(LEFT_MOTOR_B, leftB);
  analogWrite(RIGHT_MOTOR_A, rightA);
  analogWrite(RIGHT_MOTOR_B, rightB);
}

/****************************************************************************
 * Функция для установки скорости робота (линейной и угловой)
 * linearVelocity в мм/с, angularVelocity в рад/с
 ***************************************************************************/
void setRobotVelocity(float linearVelocity, float angularVelocity) {
  // Если оба параметра (линейная и угловая скорости) близки к нулю – остановка робота
  if (fabs(linearVelocity) < 10 && fabs(angularVelocity) < 0.1) {
    targetLeftWheelSpeed = 0;
    targetRightWheelSpeed = 0;
    vlSpeedFiltered = 0;
    vrSpeedFiltered = 0;
    resetPID();
    goingStraight = false;
    return;
  }

  // Если угловая скорость почти нулевая, считаем, что едем прямо
  if (fabs(angularVelocity) < 0.0001f) {
    goingStraight = true;
    leftBase = left_encoder_value;    // фиксируем текущее значение для левого энкодера
    rightBase = right_encoder_value;  // фиксируем текущее значение для правого энкодера
  } else {
    goingStraight = false;
  }

  // Вычисляем целевые скорости для левого и правого колёс по обратной кинематике
  targetLeftWheelSpeed = linearVelocity - (angularVelocity * WHEEL_BASE / 2.0);
  targetRightWheelSpeed = linearVelocity + (angularVelocity * WHEEL_BASE / 2.0);
}

/****************************************************************************
 * Парсинг команд UART
 ***************************************************************************/
bool parseSetCoeff(const String& command, float* Kp, float* Ki, float* Kd, float* Kff) {
  int index1 = command.indexOf(' ');
  if (index1 == -1) return false;
  int index2 = command.indexOf(' ', index1 + 1);
  if (index2 == -1) return false;
  int index3 = command.indexOf(' ', index2 + 1);
  if (index3 == -1) return false;
  int index4 = command.indexOf(' ', index3 + 1);
  if (index4 == -1) return false;
  *Kp = command.substring(index1 + 1, index2).toFloat();
  *Ki = command.substring(index2 + 1, index3).toFloat();
  *Kd = command.substring(index3 + 1, index4).toFloat();
  *Kff = command.substring(index4 + 1).toFloat();
  return true;
}

bool parseSetPose(const String& command, float* x, float* y, float* th) {
  int index1 = command.indexOf(' ');
  if (index1 == -1) return false;
  int index2 = command.indexOf(' ', index1 + 1);
  if (index2 == -1) return false;
  int index3 = command.indexOf(' ', index2 + 1);
  if (index3 == -1) return false;

  *x = command.substring(index1 + 1, index2).toFloat();
  *y = command.substring(index2 + 1, index3).toFloat();
  *th = command.substring(index3 + 1).toFloat();
  return true;
}

bool parseSetRobotVelocity(const String& command, float* linearVelocity, float* angularVelocity) {
  int index1 = command.indexOf(' ');
  if (index1 == -1) return false;
  int index2 = command.indexOf(' ', index1 + 1);
  if (index2 == -1) return false;
  *linearVelocity = command.substring(index1 + 1, index2).toFloat();
  *angularVelocity = command.substring(index2 + 1).toFloat();
  return true;
}

// ----------------------------------------------------------------------------
// Парсер команды SET_LED_DATA <count> <hexData>
// где <hexData> = count * 4 символов (на каждый пиксель 2 байта = 4 hex-символа).
// Пример: SET_LED_DATA 2 FFFF0F0F
// ----------------------------------------------------------------------------
void parseSetLedDataCommand(String command) {
  // 1) Находим первое пробел
  int index = command.indexOf(' ');
  if (index == -1) {
    Serial.println("ERROR: Invalid SET_LED_DATA command");
    return;
  }

  // Извлекаем подстроку после "SET_LED_DATA "
  String params = command.substring(index + 1);
  params.trim();

  // 2) Находим следующее пробел — отделить count от hexData
  int idxCount = params.indexOf(' ');
  if (idxCount == -1) {
    Serial.println("ERROR: No pixel count in SET_LED_DATA");
    return;
  }

  // Читаем count
  String countStr = params.substring(0, idxCount);
  int pixelCount = countStr.toInt();
  if (pixelCount < 1 || pixelCount > NUM_PIXELS) {
    Serial.println("ERROR: pixelCount out of range");
    return;
  }

  // Оставшаяся часть — hexData
  String hexData = params.substring(idxCount + 1);
  hexData.trim();

  // Проверим длину hexData
  // На каждый пиксель нужно 4 hex-символа (2 байта),
  // значит всего нужно (pixelCount * 4) символов.
  int requiredLen = pixelCount * 4;
  if (hexData.length() < requiredLen) {
    Serial.println("ERROR: hexData too short");
    return;
  }

  // 3) Парсим hexData по 4 символа на каждый пиксель
  for (int i = 0; i < pixelCount; i++) {
    // Читаем 4 hex-символа
    String chunk = hexData.substring(i * 4, i * 4 + 4);

    // Преобразуем в 16-битное число
    uint16_t colorVal = (uint16_t)strtol(chunk.c_str(), NULL, 16);

    // Распаковываем (R4, G4, B4, Br)
    uint8_t R4 = (colorVal >> 12) & 0x0F;  // старшие 4 бита
    uint8_t G4 = (colorVal >> 8) & 0x0F;
    uint8_t B4 = (colorVal >> 4) & 0x0F;
    uint8_t Br = colorVal & 0x0F;

    // Преобразуем в 8-битные
    // Сначала 0..15 конвертируем в 0..255, потом масштабируем на Brightness (Br)
    // Т.е. (R4 * 255/15) -> R8base, затем R8 = R8base * (Br/15)
    uint8_t R8base = (R4 * 255) / 15;
    uint8_t G8base = (G4 * 255) / 15;
    uint8_t B8base = (B4 * 255) / 15;

    uint8_t R8 = (uint8_t)((R8base * Br) / 15);
    uint8_t G8 = (uint8_t)((G8base * Br) / 15);
    uint8_t B8 = (uint8_t)((B8base * Br) / 15);

    // Устанавливаем цвет пикселя в ленте
    ws2812b.setPixelColor(i, ws2812b.Color(R8, G8, B8));
  }

  // Если нужно очистить остаток ленты, если передано < NUM_PIXELS
  for (int i = pixelCount; i < NUM_PIXELS; i++) {
    ws2812b.setPixelColor(i, 0);  // выключим
  }

  // 4) Обновляем ленту одним вызовом для скорости
  ws2812b.show();

  // Сообщаем об успехе
  Serial.println("OK");
}


void waitingAnimation() {
  static uint32_t ledTimer = millis();
  static uint8_t hsv = 0;
  static uint8_t currentPixel = 0;
  if (millis() - ledTimer > 50) {
    ws2812b.setPixelColor(currentPixel, ws2812b.ColorHSV(hsv * 255, 255, 50));
    ws2812b.show();
    hsv += 2;
    currentPixel++;
    if (currentPixel >= NUM_PIXELS) currentPixel = 0;
    ledTimer = millis();
  }
}




/****************************************************************************
 * Обработка команд из UART
 ***************************************************************************/
void processCommand(String command) {
  command.trim();
  if (command.equalsIgnoreCase("PING")) {
    Serial.println("ROBOT_001");
    for (int i = 0; i < NUM_PIXELS; i++) {
      ws2812b.setPixelColor(i, 0);  // выключим ленту
    }
    ws2812b.show();
    bootMode = 0;
  } else if (command.startsWith("SET_POSE")) {
    float x, y, th;
    if (parseSetPose(command, &x, &y, &th)) {
      xPos = x;
      yPos = y;
      theta = th;
      Serial.println("OK: Pose set");
    }
    Serial.println("OK: Pose set");
  } else if (command.startsWith("SET_COEFF")) {
    float newKp, newKi, newKd, newKff;
    if (parseSetCoeff(command, &newKp, &newKi, &newKd, &newKff)) {
      pidKp = newKp;
      pidKi = newKi;
      pidKd = newKd;
      pidKff = newKff;
      Serial.println("OK: Coefficients updated");
    } else {
      Serial.println("ERROR: Invalid coefficients");
    }
  } else if (command.startsWith("SET_ROBOT_VELOCITY")) {
    float linVel = 0.0, angVel = 0.0;
    if (parseSetRobotVelocity(command, &linVel, &angVel)) {
      setRobotVelocity(linVel, angVel);
      Serial.println("OK: Robot velocity set");
    } else {
      Serial.println("ERROR: Invalid robot velocity command");
    }
  } else if (command.startsWith("SET_LED_DATA")) {
    parseSetLedDataCommand(command);
  } 

  else {
    Serial.println("ERROR: Unknown command");
  }
}

/****************************************************************************
 * setup() и loop()
 ***************************************************************************/
void setup() {
  Serial.begin(115200);
  delay(1000);
  Serial.println("System started");

  //Serial1.begin(SERVO_BAUD, SERIAL_8N1, S_RXD, S_TXD);
  //st.pSerial = &Serial1;


  attachInterrupt(digitalPinToInterrupt(LEFT_ENCODER_A), left_interrupt, RISING);
  attachInterrupt(digitalPinToInterrupt(RIGHT_ENCODER_A), right_interrupt, RISING);

  pinMode(LEFT_MOTOR_A, OUTPUT);
  pinMode(LEFT_MOTOR_B, OUTPUT);
  pinMode(RIGHT_MOTOR_A, OUTPUT);
  pinMode(RIGHT_MOTOR_B, OUTPUT);

  pinMode(LEFT_ENCODER_A, INPUT);
  pinMode(LEFT_ENCODER_B, INPUT);
  pinMode(RIGHT_ENCODER_A, INPUT);
  pinMode(RIGHT_ENCODER_B, INPUT);

  // Инициализируем NeoPixel
  ws2812b.begin();
  ws2812b.setBrightness(LED_BRIGHTNESS);
  ws2812b.clear();
  ws2812b.show();
}

void loop() {
  if (Serial.available()) {
    String command = Serial.readStringUntil('\n');
    processCommand(command);
  }

  updateOdometry();

  static uint32_t PIDTimer = 0;
  if (millis() - PIDTimer > 50) {
    computeSpeed();
    computeWheelsPID();
    PIDTimer = millis();
  }

  static uint32_t printTimer = 0;
  if (millis() - printTimer > 200 and !bootMode) {
    Serial.printf("POS X=%.2f Y=%.2f Th=%.2f ", xPos, yPos, theta);
    Serial.printf("ENC L=%ld R=%ld ", left_encoder_value, right_encoder_value);
    Serial.printf("SPD L=%.2f mm/s R=%.2f mm/s ", vlSpeedFiltered, vrSpeedFiltered);
    Serial.printf("Target L=%.2f mm/s R=%.2f mm/s\n", targetLeftWheelSpeed, targetRightWheelSpeed);
    printTimer = millis();
  }

  if (bootMode == 1) { waitingAnimation(); }
}

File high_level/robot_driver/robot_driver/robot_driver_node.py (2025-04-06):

#!/usr/bin/env python3

import rclpy
from rclpy.node import Node

from geometry_msgs.msg import Twist
from nav_msgs.msg import Odometry
from geometry_msgs.msg import TransformStamped

import tf2_ros
import serial
import re
from transforms3d.euler import euler2quat

class RobotDriverNode(Node):
    def __init__(self):
        super().__init__('robot_driver_node')

        # 1. Подписка на /cmd_vel для приёма скоростей
        self.cmd_vel_sub = self.create_subscription(
            Twist,
            '/cmd_vel',
            self.cmd_vel_callback,
            10
        )

        # 2. Паблишер одометрии
        self.odom_pub = self.create_publisher(Odometry, 'odom', 10)

        # 3. TF Broadcaster
        self.tf_broadcaster = tf2_ros.TransformBroadcaster(self)

        # 4. Открываем Serial-порт
        #    ВАЖНО: подставьте свой реальный путь к Serial!
        serial_port_path = "/dev/serial/by-path/platform-xhci-hcd.0-usbv2-0:2:1.0"
        self.ser = serial.Serial(serial_port_path, baudrate=115200, timeout=0.1)
        self.get_logger().info(f"Opened serial port: {serial_port_path}")

        # 5. Регулярка для парсинга строк вида: "POS X=120.00 Y=150.00 Th=0.45"
        self.pos_pattern = re.compile(r'POS X=([\-\d\.]+) Y=([\-\d\.]+) Th=([\-\d\.]+)')

        # 6. Периодический таймер для чтения данных из Serial
        self.timer_period = 0.05  # 20 Гц
        self.read_serial_timer = self.create_timer(self.timer_period, self.read_serial_timer_callback)

    def cmd_vel_callback(self, msg: Twist):
        """
        Колбэк, вызывается при приходе сообщения в /cmd_vel
        Отправляем команду скорости на ESP32 по Serial.
        """
        linear_velocity = msg.linear.x * 1000.0  # м/с -> мм/с
        angular_velocity = msg.angular.z         # рад/с

        command = f"SET_ROBOT_VELOCITY {linear_velocity:.2f} {angular_velocity:.2f}\n"
        try:
            self.ser.write(command.encode())
            self.get_logger().info(f"Sent command: {command.strip()}")
        except serial.SerialException as e:
            self.get_logger().error(f"Failed to write to serial: {e}")

    def read_serial_timer_callback(self):
        """
        Периодически читаем строки из Serial.
        Если строка похожа на POS X=... Y=... Th=..., парсим и публикуем одометрию + TF.
        """
        # Считываем всё, что накопилось в буфере (т.к. timeout=0.1)
        try:
            # Можем читать построчно, т.к. ESP32 шлёт строки.
            line = self.ser.readline().decode('ascii', errors='ignore').strip()

            if not line:
                return  # нет данных в данный момент

            # Проверим, похоже ли это на строку одометрии
            match = self.pos_pattern.search(line)
            if match:
                x_mm = float(match.group(1))  # мм
                y_mm = float(match.group(2))  # мм
                th   = float(match.group(3))  # рад

                # Переводим мм -> м
                x = x_mm / 1000.0
                y = y_mm / 1000.0

                # Формируем Odometry
                odom_msg = Odometry()
                odom_msg.header.stamp = self.get_clock().now().to_msg()
                odom_msg.header.frame_id = 'odom'
                odom_msg.child_frame_id = 'base_link'

                odom_msg.pose.pose.position.x = x
                odom_msg.pose.pose.position.y = y
                odom_msg.pose.pose.position.z = 0.0

                # Преобразуем угол в кватернион
                q = euler2quat(0.0, 0.0, th)  # returns (w, x, y, z) - такая у transforms3d специфика
                odom_msg.pose.pose.orientation.w = q[0]
                odom_msg.pose.pose.orientation.x = q[1]
                odom_msg.pose.pose.orientation.y = q[2]
                odom_msg.pose.pose.orientation.z = q[3]

                # Публикуем в топик /odom
                self.odom_pub.publish(odom_msg)

                # Одновременно шлём TF odom -> base_link
                t = TransformStamped()
                t.header.stamp = odom_msg.header.stamp
                t.header.frame_id = 'odom'
                t.child_frame_id = 'base_link'
                t.transform.translation.x = x
                t.transform.translation.y = y
                t.transform.translation.z = 0.0
                t.transform.rotation.w = q[0]
                t.transform.rotation.x = q[1]
                t.transform.rotation.y = q[2]
                t.transform.rotation.z = q[3]

                self.tf_broadcaster.sendTransform(t)

                # Для наглядности выведем в лог
                self.get_logger().info(f"ODOM: X={x:.3f} Y={y:.3f} Th={th:.3f}")
            else:
                # Можно выводить предупреждение, но чтобы не заспамить лог, сделаем debug
                self.get_logger().debug(f"Unknown line: {line}")

        except serial.SerialException as e:
            self.get_logger().error(f"Failed to read from serial: {e}")

def main(args=None):
    rclpy.init(args=args)
    node = RobotDriverNode()
    rclpy.spin(node)
    node.destroy_node()
    rclpy.shutdown()

if __name__ == '__main__':
    main()
